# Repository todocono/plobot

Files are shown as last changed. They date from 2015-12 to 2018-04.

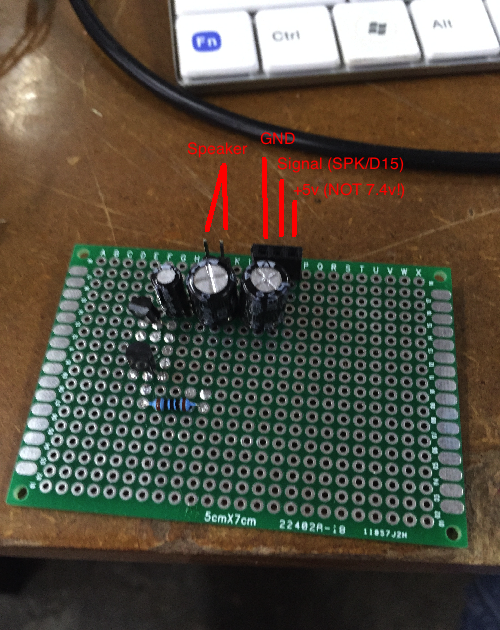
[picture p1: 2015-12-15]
audio_test/prototype.png

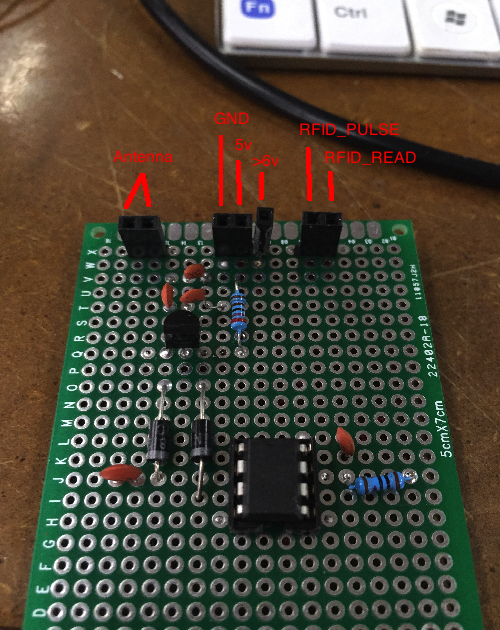
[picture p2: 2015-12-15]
RFIDTest/prototype.png

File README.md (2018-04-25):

# ATTENTION: Files here are deprecated

Plobot is a project started in 2015 by Camilo Parra Palacios and Rodolfo Cossovich. The project website is hosted at http://plobot.com

This repository had various contributors, mainly Sean, Ivan and Arlen. I moved files for maintenance to the repositories:

https://github.com/todocono/Plobot-PCB
https://github.com/todocono/Plobot-ID
https://github.com/todocono/Plobot-soft

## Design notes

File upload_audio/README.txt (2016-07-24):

To write a binary file to the Plobot's flash chip on OSX: 

1. Connect FTDI. Have bootloader installed on Atmega644P. 
2. Upload arduino_stream.ino to the Atmega644P. 
3. Run "goSerial". Set modem port (/dev/something) to 57600 baud rate and press connect
	Note that you should see "---- Streaming Upload ready ----" in the window.
4. Build + run upload_stream.cc
	For example: g++ -o upload_stream ./upload_stream.cc
				 upload_stream ../audio_test/mambo.pcm /dev/cu.usbmodem1421 NORMAL
5. Watch goSerial for error messages. Note that "unknown command" means that the XSP device needs an initial character to get it out of command mode. Use "XSP" instead of "NORMAL" in your upload_stream command.

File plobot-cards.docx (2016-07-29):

Card functions

English | 名字 | Spanish | Description | Special Function
Start | 开始 | Empezar | Starts the sequential program | n/a
Reset | 重置 | Resetear | Pauses the execution of the program. If it is not running, it will clear the memory. | n/a
Go Ahead | 前进 | Adelante | Moves one step forward (about 15cm) | Moves a small step forward ( 5cm?)
Turn Left | 左转 | Gira a la izquierda | Turns 90 degrees left | Turns a small step (15 degrees)
Turn Right | 右转 | Gira a la derecha | Turns 90 degrees right | Turns a small step (15 degrees)
Go Back | 后退 | Atras | Moves one step backward (about 15cm) | Moves a small step backward ( 5cm?)
Lift | 手臂 | Levantar | Toggles both servos position 0/ 90 /90 degrees. | Toggles both servos position within 15 degrees . Till 180 and comes back
Listen | 听 | Escuchar | It has a logic output of YES/NO referred to a clap | It has the opposite logic
See | 探测 | Detectar | It has a logic output of YES/NO referred to a 5cm obstacle | It has the opposite logic
Feel | 触摸 | Sentir | It has a logic output of YES/NO referred to a big inclination change (shake or double tap would work) | It has the opposite logic

Note 1: colors combine with each other. Intensity modifies if followed by a value.

Note 2: (for future versions) all parameters are normalized between a 0 and 10, or a min and max. In the case of musical notes Do, Re, Mi, Fa, Sol, La, Si and Do, Re, Mi of the following octave.

Note 3: Servos are detached when not moving.

Note 4: Need a visual/audio indication when: card is read, program is executing, battery is low

Spells

Repeat | 重复 | Repetir | It reproduces a chunk of code. If followed by a sequence of store/code/store, it redefines the function. If it has a repeat inside of it's own definition, it loops forever. | idem
Store | 储存 | Guardar | If preceded by Repeat, Starts / ends the content of Repeat function. It works as brackets. If preceded by Sound, it stores a sound in the internal memory. | idem
Random | 随机 | Azar | Gives a random number that affects the behavior of the last order.
Teach | 教学 | Enseñar | Teaches a set of movements
Boost | 更改 | Especial | Modifies other functions. It stays ON only for one card. It modifies the way that the light glows. | Sets Boost like a caps lock.
Pause / Freeze | 暂停 | Pausa | Waits for 1s | Waits for 10s
Sound | 声音 | Sonido | Alone, it plays the sound recorded. If followed by Store, allows to save a new recorded sound. | It has some pre-recorded sounds.

7 colors of rainbow

Red | 红色 | Rojo | Turns ON led to glow Red. | Blinking Red
Green | 绿色 | Verde | Turns ON led to glow Green | Blinking Green
Orange | 橙色 | Naranja | Turns ON led to glow | Blinking
Yellow | 黄色 | Amarillo | Turns ON led to glow | Blinking
Pink | 靛蓝 | Rosa | Turns ON led to glow | Blinking
Purple | 紫色 | Violeta | Turns ON led to glow | Blinking
Blue | 蓝色 | Azul | Turns ON led to glow Blue | Blinking Blue

7 notes of music

do | do | | Piano do | Bemol or Sharp?
re | re
mi | mi
fa | fa
sol | sol
la | la
si | si

learning by demonstration

similar to behavior

demonstrating the kinetic

mode to teach the robot movements

custom capabilities

IMU with encoders

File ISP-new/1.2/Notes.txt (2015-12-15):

2011.08.26:
	- Para programar DuinoBot.v1.x con el AVRDoper que está en RobotGroup, utilizar el siguiente BAT:
		DuinoBot.bat
		
	- Para programar DuinoBot.v1.x el USBasp mío, utilizar el siguiente BAT:
		DuinoBot.USBAsp.bat
		
	- Para programar DuinoBot.Kids.v1.x con el AVRDoper que está en RobotGroup, utilizar el siguiente BAT:
		- Kids.bat

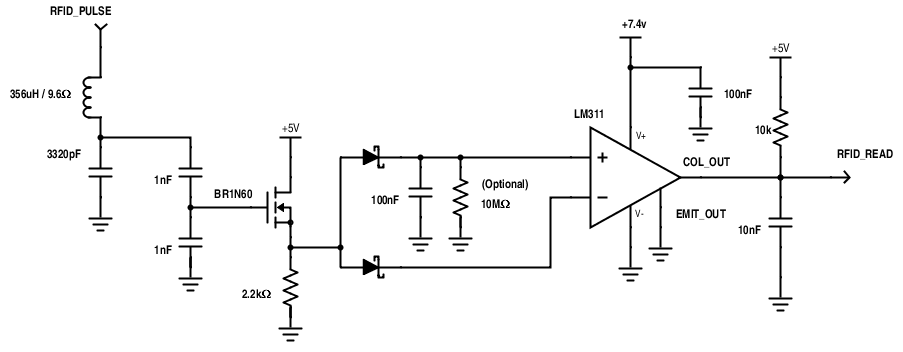
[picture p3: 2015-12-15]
RFIDTest/schematic.png

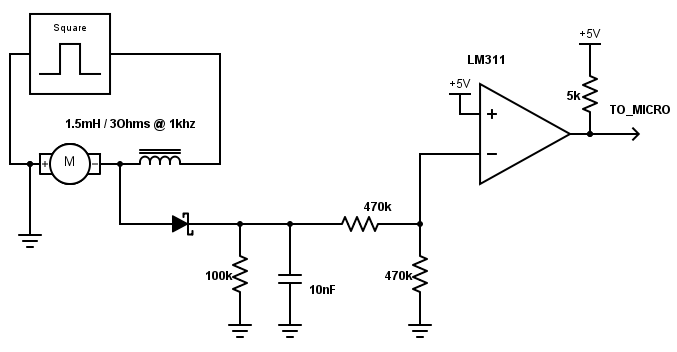
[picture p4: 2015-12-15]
back_emf_test/circuit_schematic.png

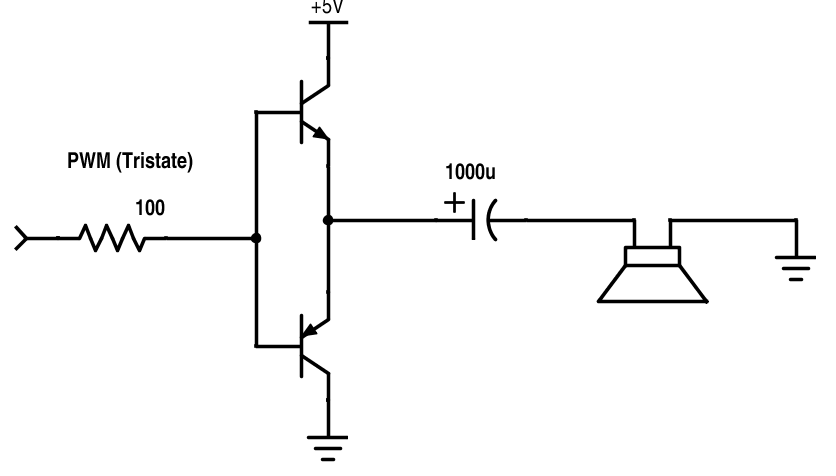
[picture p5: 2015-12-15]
audio_test/schematic.png

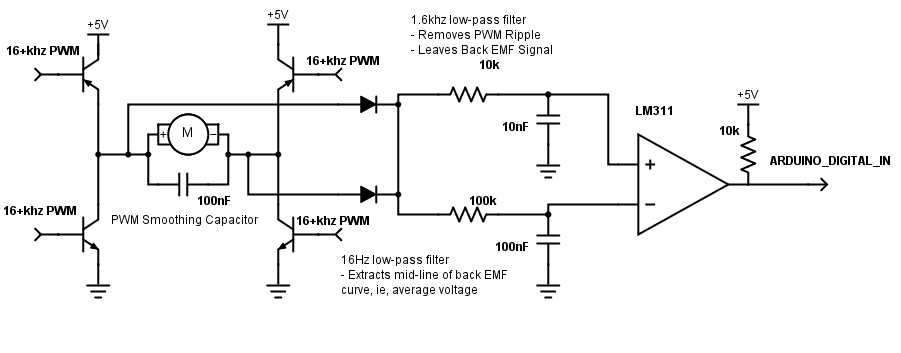
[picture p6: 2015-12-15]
Back-EMF-Sense.png

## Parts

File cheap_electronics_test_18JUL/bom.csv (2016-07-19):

Comment | Description | Designator | Footprint | LibRef | Quantity
18pF | Capacitor | C1, C4 | CAPC1608N | Cap | 2
10uF | Capacitor | C2, C3 | CAPC1608N | Cap | 2
10uF | Capacitor | C5, C? | CAPC3216L | Cap | 2
100nF | Capacitor | C6, C7 | CAPC1608N | CAP | 2
3320pF | Capacitor | C8 | CAPC1608N | Cap | 1
1uF | Capacitor | C9 | CAPC1608N | Cap | 1
MBR0540 | Default Diode | D1, D2, D3, D5, D6, D7, D8, D9 | SOD123/X.85 | Diode | 8
LED3 | Typical BLUE SiC LED | D4 | CAPC1608N | LED3 | 1
XSP | Header, 4-Pin, Dual row, Right Angle | J1 | HDR2X4H | Header 4X2H | 1
Header 2H | Header, 2-Pin, Right Angle | JANT (1, JLOAD1, JPWR1 | HDR1X2H | Header 2H | 3
Header 5H | Header, 5-Pin, Right Angle | JDBG1 | HDR1X5H | Header 5H | 1
BSS806N |  | Q1, Q2, Q3, Q4, Q5, Q6, Q7, Q8, Q9, Q10, Q11 | BSS806N | BSS806N | 11
10k | Resistor | R1, R2, R11, R12, R20 | RESC1608N | Res2 | 5
300 | Resistor | R3 | RESC1608N | Res2 | 1
100 | Resistor | R4, R5, R6, R8, R9, R13, R14, R15, R21 | RESC1608N | Res2 | 9
10 | Resistor | R7 | RESC1608N | Res2 | 1
50 | Resistor | R10 | RESC1608N | Res2 | 1
100k | Resistor | R16 | RESC1608N | Res2 | 1
1k | Resistor | R17, R18, R19 | RESC1608N | Res2 | 3
ATmega644A-AU | 8-bit AVR Microcontroller, 64KB Flash, 2KB EEPROM, 4KB SRAM, 44-pin TQFP, Industrial Grade (-40°C to 85°C) | U1 | 44A_N | ATmega644A-AU | 1
ABM7-8.000MHZ-D2Y-T |  | XTAL1 | XTAL | ABM7-8.000MHZ-D2Y-T | 1

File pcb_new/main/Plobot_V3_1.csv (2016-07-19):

Comment | Description | Designator | Footprint | LibRef | Quantity
ON/OFF |  | B1 | KGPS22F03 | Component_1 | 1
100nF | Capacitor | C1, C3, C6, C7, C8, C12, C13, C14, C15, C16, C18, C19, C21, C26, C27, C28, C29, C32, C34, C35, C37, C38, C48 | CAPC1608N | Cap | 25
18pF | Capacitor | C2, C4 | CAPC1608N | Cap | 2
10 uF | Capacitor | C5, C11 | CAPC3216N | Cap_2 | 2
15pF | Capacitor | C9, C10, C22, C45 | CAPC1608N | CAP | 4
10uF | Capacitor | C17, C23, C31, C51 | CAPC3216N | Cap_2 | 4
47pF | Capacitor | C24, C42 | CAPC1608N | CAP | 2
10nF/16V | Capacitor | C25, C33 | CAPC2012N | Cap | 2
2.2uF | Capacitor | C30, C39 | CAPC2012N | Cap, Cap_2 | 2
1uF | Capacitor | C36 | CAPC2012N | Cap_2 | 1
180pF | Capacitor | C40, C43 | CAPC1608N | CAP | 2
10pF | Capacitor | C41, C44 | CAPC1608N | CAP | 2
MBR0540 | Default Diode | D1 | SOD123/X.85 | Diode | 1
LED3 | Typical BLUE SiC LED | DLED | LED 0603/1608 BLUE | LED3 | 1
miniSMDC260F/12 | Thermal Fuse | F1, F2 | miniSMDC260F/12 | Fuse Thermal | 2
XSP | Header, 4-Pin, Dual row, Right Angle | J1 | HDR2X4H | Header 4X2H | 1
Header 15 | Header, 15-Pin | JBOTTOM | B15B-XH-A | Header 15 | 1
Charger |  | JCHG1 | S3B-XH-A(LF)(SN) | BATTCON | 1
Header 5 | Header, 5-Pin | JDBG | HDR1X5 | Header 5 | 1
Header 4 | Header, 4-Pin | JI2C, JSPI | HDR1X4 | Header 4 | 2
Header 7 | Header, 7-Pin | JTOP | B7B-XH-A | Header 7 | 1
10uH | Inductor | L1 | INDC1608N | Inductor | 1
2.2uH | Inductor | L2, L3 | INDC1608N | Inductor | 2
Mic2 | Microphone | MK1 | electret_6mm | Mic2 | 1
10k | Resistor | R1, R2, R4, R5, R6, R7, R9, R12, R13, R14, R17, R18, R22 | RESC1608N | Res2 | 13
20k | Resistor | R3 | RESC1608N | Res2 | 1
100k | Resistor | R8 | RESC1608N | Res2 | 1
3.3k | Resistor | R10 | RESC1608N | Res2 | 1
22 | Resistor | R11 | RESC1608N | Res2 | 1
820 | Resistor | R15 | RESC1608N | Res2 | 1
5.1k | Resistor | R16, R20, R21 | RESC1608N | Res2 | 3
1K | Resistor | R19, R23 | RESC1608N | Res2 | 2
470 | Resistor | R27 | RESC1608N | Res2 | 1
1 | Resistor | R28 | RESC1608N | Res2 | 1
MCU | 8-bit AVR Microcontroller, 2.7-5.5V, 20MHz, 64KB Flash, 2KB EEPROM, 4KB SRAM, 44-pin TQFP | U1 | atmega644p | ATmega644-20AU | 1
LM358D | Dual Operational Amplifier | U2 | LM358D | LM358D | 1
W25Q64BVSIG |  | U3 | W25Q64BVSIG | W25Q64BVSIG | 1
SN74HC04D | Hex Inverter | U4 | D014_N | SN74HC04D | 1
AZ1117CH-3.3 |  | U5 | SOT223 | LM1117 | 1
SN74HC08D | Quadruple 2-Input Positive-AND Gate | U8, U14 | D014_N | SN74HC08D | 2
DRV8833 |  | U9, U12 | DRV8833 | DRV8833 | 2
ITR9608 + 2x 额外的塑料片 |  | U10, U11 | ITR9608 | ITR9608 + 2x 额外的塑料片 | 2
ADXL345BCCZ |  | U13 | ADXL345 | ADXL345 | 1
AZ1084CD-5.0 |  | U101 | AZ1084CD-5.0 | AZ1084CD-5.0 | 1
WS2812B |  | ULED_INNER, ULED_OUTER1, ULED_OUTER2, ULED_OUTER3, ULED_OUTER4 | WS2812B | WS2812B | 5
MFRC52202HN1 |  | URFID | MFRC52202HN1 | MFRC52202HN1 | 1
7A-27.120MAAJ-T |  | XRFID | XTAL | Tm08B.S01_12M_42 | 1
ABM7-8.000MHZ-D2Y-T |  | XTAL1 | XTAL | ABM7-8.000MHZ-D2Y-T | 1

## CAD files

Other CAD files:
pcb_mechanical.DXF

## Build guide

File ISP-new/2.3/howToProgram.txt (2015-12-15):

::DuinoBot.v2.3::

1. First program the ATMega16U2: connect the USBasp to its ISP connector, and run DuinoBot.mega16U2.USBAsp.bat.
2. Second program the ATMega1284p: connect the USBasp to its ISP connector, and run DuinoBot.mega1284.USBAsp.bat.
3. Finally, run the test protocol with DuinoPack.v1.0 (can be downloaded from this link: http://multiplo.org/category/software/).

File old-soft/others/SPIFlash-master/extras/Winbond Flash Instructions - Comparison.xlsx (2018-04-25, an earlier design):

Characteristics | W25X05CL | W25X10BV | W25X20BV | W25X40BV | W25Q80BV | W25Q16BV | W25Q32BV | W25Q64BV | W25Q128BV | W25Q256FV
Size (Bits) | 512K-Bit | 1M-Bit | 2M-Bit | 4M-Bit | 8M-Bit | 16M-Bit | 32M-Bit | 64M-Bit | 128M-Bit | 256M-Bit
Size (Bytes) | 64K-Byte | 128K-Byte | 256K-Byte | 512K-Byte | 1M-Byte | 2M-Byte | 4M-Byte | 8M-Byte | 16M-Byte | 32M-Byte
Programming size | 64L*1024L | 128L*1024L | 256L*1024L | 512L*1024L | 1L*1024L*1024L | 2L*1024L*1024L | 4L*1024L*1024L | 8L*1024L*1024L | 16L*1024L*1024L | 32L*1024L*1024L
No. of pages | 256 | 512 | 1024 | 2048 | 4096 | 8192 | 16384 | 32768 | 65536 | 131072
Voltage | 2.5V - 3.3V | 2.7V - 3.6V | 2.7V - 3.6V | 2.7V - 3.6V | 2.5V - 3.6V | 2.7V to 3.6V | 2.7V to 3.6V | 2.7V to 3.6V | 2.7V to 3.6V | 2.7V to 3.6V
Current (Active) | 1mA | 4mA | 4mA | 4mA | 4mA | 4mA | 4mA | 4mA | 4mA | 4mA
Current (Power-down) | < 1µA | < 1µA | < 1µA | < 1µA | < 1µA | < 1µA | < 1µA | < 1µA | < 1µA | < 1µA
Sector size | 4KB | 4KB | 4KB | 4KB | 4KB | 4KB | 4KB | 4KB | 4KB | 4KB
No. of sectors | 16 | 32 | 64 | 128 | 256 | 512 | 1024 | 2048 | 4096 | 8192
No. of 32K blocks | 2 | 4 | 8 | 16 | 32 | 64 | 128 | 256 | 512 | 1024
No. of 64K blocks | 1 | 2 | 4 | 8 | 16 | 32 | 64 | 128 | 256 | 512
I/O | SPI, DUAL I/O | SPI, Dual Outputs, Dual I/O | SPI, Dual Outputs, Dual I/O | SPI, Dual Outputs, Dual I/O | SPI, Dual SPI, Quad SPI | SPI, Dual SPI, Quad SPI | SPI, Dual SPI, Quad SPI | SPI, Dual SPI, Quad SPI | SPI, Dual SPI, Quad SPI | SPI, Dual SPI, Quad SPI
Max clock speed | 104MHz | 104MHz | 104MHz | 104MHz | 104MHz | 104MHz | 104MHz | 80MHz | 104MHz
Page Program | YES | YES | YES | YES | YES | YES | YES | YES | YES | YES
Identification
Manufacturer ID | EFh | EFh | EFh | EFh | EFh | EFh | EFh | EFh | EFh | EFh
Device ID
Byte 1 (Manufacturer ID) | EFh | EFh | EFh | EFh | EFh | EFh | EFh | EFh | EFh | EFh
Byte 2 (Memory Type) | 05h | 10h | 11h | 12h | 13h | 14h | 15h | 16h | 17h | 18h
Byte 3 (Capacity) | 3010h | 3011h | 3012h | 3013h | 4014h | 4015h | 4016h | 4017h | 4018h | 4019h
Instructions
Write Enable | 06h | 06h | 06h | 06h | 06h | 06h | 06h | 06h | 06h | 06h
Write Enable for Volatile Status Register | 50h | - | - | - | 50h | - | 50h | - | 50h | 50h
Write Disable | 04h | 04h | 04h | 04h | 04h | 04h | 04h | 04h | 04h | 04h
Read Status Register 1 | 05h | 05h | 05h | 05h | 05h | 05h | 05h | 05h | 05h | 05h
Read Status Register 2 | - | - | - | - | 35h | 35h | 35h | 35h | 35h | 35h
Write Status Register 1 | 01h | 01h | 01h | 01h | 01h | 01h | 01h | 01h | 01h | 01h
Write Status Register 2 |  |  |  |  |  |  |  |  |  | 31h
Write Status Register 3 |  |  |  |  |  |  |  |  |  | 11h
Read Extended Addr. Register |  |  |  |  |  |  |  |  |  | C8h
Write Extended Addr. Register |  |  |  |  |  |  |  |  |  | C5h
Read Data | 03h | 03h | 03h | 03h | 03h | 03h | 03h | 03h | 03h | 03h
Fast Read | 0Bh | 0Bh | 0Bh | 0Bh | 0Bh | 0Bh | 0Bh | 0Bh | 0Bh | 0Bh
Fast Read Dual Output | 3Bh | 3Bh | 3Bh | 3Bh | 3Bh | 3Bh | 3Bh | 3Bh | 3Bh | 3Bh
Fast Read Dual I/O | BBh | BBh | BBh | BBh | BBh | BBh | BBh | BBh | BBh | BBh
Fast Read Quad Output | - | - | - | - | 6Bh | 6Bh | 6Bh | 6Bh | 6Bh | 6Bh
Fast Read Quad I/O | - | - | - | - | EBh | EBh | EBh | EBh | EBh | EBh
Word Read Quad I/O | - | - | - | - | E7h | E7h | E7h | - | E7h | E7h
Octal Word Read Quad I/O | - | - | - | - | E3h | E3h | E3h | E3h | E3h | E3h
Set Burst with wrap | - | - | - | - | 77h | - | 77h | - | 77h | 77h
Page Program | 02h | 02h | 02h | 02h | 02h | 02h | 02h | 02h | 02h | 02h
Quad Page Program | - | - | - | - | 32h | 32h | 32h | 32h | 32h | 32h
Sector Erase (4KB) | 20h | 20h | 20h | 20h | 20h | 20h | 20h | 20h | 20h | 20h
Block Erase (32KB) | 52h | 52h | 52h | 52h | 52h | 52h | 52h | 52h | 52h | 52h
Block Erase (64KB) | D8h | D8h | D8h | D8h | D8h | D8h | D8h | D8h | D8h | D8h
Chip Erase | C7h/60h | C7h/60h | C7h/60h | C7h/60h | C7h/60h | C7h/60h | C7h/60h | C7h/60h | C7h/60h | C7h/60h
Erase/Program suspend | - | - | - | - | 75h | 75h | 75h | 75h | 75h | 75h
Erase/Program resume | - | - | - | - | 7Ah | 7Ah | 7Ah | 7Ah | 7Ah | 7Ah
Contiuous Read Mode | - | - | - | - | FFh | FFh | FFh | FFh | FFh | FFh
High Performance Mode | - | - | - | - | - | - | - | A3h | - | -
Power-down | B9h | B9h | B9h | B9h | B9h | B9h | B9h | B9h | B9h | B9h
Release Power-down/ Device ID | ABh | ABh | ABh | ABh | ABh | ABh | ABh | ABh | ABh | ABh
Manufacturer/Device ID | 90h | 90h | 90h | 90h | 90h | 90h | 90h | 90h | 90h | 90h
Manufacturer/Device ID by Dual I/O | 92h | 92h | 92h | 92h | 92h | 92h | 92h | - | 92h | 92h
Manufacturer/Device ID by Quad I/O | - | - | - | - | 94h | 94h | 94h | - | 94h | 94h
JEDEC ID | 9Fh | 9Fh | 9Fh | 9Fh | 9Fh | 9Fh | 9Fh | 9Fh | 9Fh | 9Fh
Read Unique ID | 4Bh | 4Bh | 4Bh | 4Bh | 4Bh | 4Bh | 4Bh | 4Bh | 4Bh | 4Bh
Read SDFP Register | - | - | - | - | 5Ah | - | 5Ah | - | 5Ah
Erase Security Registers | - | - | - | - | 44h | - | 44h | - | 44h
Program Security Registers | - | - | - | - | 42h | - | 42h | - | 42h
Read Security Registers | - | - | - | - | 48h | - | 48h | - | 48h
Global Block Lock |  |  |  |  |  |  |  |  |  | 7Eh
Global Block Unlock |  |  |  |  |  |  |  |  |  | 98h
Individual Block Lock |  |  |  |  |  |  |  |  |  | 36h
Individual Block Unlock |  |  |  |  |  |  |  |  |  | 39h
Read Block Lock |  |  |  |  |  |  |  |  |  | 3Dh

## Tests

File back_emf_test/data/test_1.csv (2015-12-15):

EMF | Encoder
101.00 | 26.00
416.00 | 29.00
874.00 | 40.00
1222.00 | 52.00
1552.00 | 63.00
1836.00 | 77.00
2172.00 | 89.00
2462.00 | 101.00
2760.00 | 113.00
3074.00 | 125.00
3366.00 | 138.00
3688.00 | 150.00
4042.00 | 165.00
4417.00 | 180.00
1.00 | 7.00
0.00 | 0.00
0.00 | 0.00
0.00 | 0.00
0.00 | 0.00
0.00 | 0.00
0.00 | 0.00
1746.00 | 72.00
2048.00 | 86.00
2412.00 | 99.00
2736.00 | 112.00
3050.00 | 125.00
3322.00 | 136.00
3660.00 | 149.00
4040.00 | 165.00
4370.00 | 179.00
2.00 | 9.00
0.00 | 0.00
0.00 | 0.00
0.00 | 0.00
0.00 | 0.00
0.00 | 0.00
0.00 | 0.00
0.00 | 0.00
782.00 | 32.00
1162.00 | 47.00
1196.00 | 45.00
1530.00 | 57.00
1860.00 | 69.00
1974.00 | 76.00
2336.00 | 89.00
2564.00 | 99.00
0.00 | 2.00
0.00 | 0.00
0.00 | 0.00
0.00 | 0.00
620.00 | 27.00
830.00 | 34.00
1068.00 | 42.00
1286.00 | 49.00
1554.00 | 59.00
2212.00 | 87.00
3124.00 | 130.00

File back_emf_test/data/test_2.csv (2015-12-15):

EMF | Encoder
0.00 | 0.00
0.00 | 0.00
0.00 | 0.00
0.00 | 0.00
1640.00 | 67.00
1991.00 | 82.00
2255.00 | 92.00
2526.00 | 104.00
2891.00 | 118.00
3193.00 | 132.00
3500.00 | 143.00
3769.00 | 155.00
4133.00 | 169.00
4496.00 | 185.00
0.00 | 7.00
0.00 | 0.00
180.00 | 21.00
482.00 | 32.00
935.00 | 44.00
1291.00 | 54.00
1650.00 | 68.00
2006.00 | 83.00
2262.00 | 92.00
2590.00 | 107.00
2890.00 | 118.00
3204.00 | 132.00
3486.00 | 143.00
3810.00 | 156.00
4194.00 | 171.00
4561.00 | 186.00
1.00 | 7.00
0.00 | 0.00
0.00 | 0.00
0.00 | 0.00
0.00 | 0.00
1326.00 | 59.00
1708.00 | 71.00
1956.00 | 80.00
2188.00 | 90.00
2550.00 | 105.00
2878.00 | 118.00
3228.00 | 131.00
3522.00 | 143.00
3834.00 | 156.00
4174.00 | 171.00
4581.00 | 186.00
1.00 | 8.00
0.00 | 0.00
0.00 | 0.00
0.00 | 0.00
62.00 | 3.00
652.00 | 31.00
674.00 | 28.00
984.00 | 41.00
1220.00 | 50.00
1418.00 | 58.00
1743.00 | 71.00
1861.00 | 76.00
2188.00 | 89.00
2338.00 | 95.00
2483.00 | 102.00
2231.00 | 91.00
0.00 | 3.00
0.00 | 0.00
22.00 | 2.00
254.00 | 12.00
320.00 | 15.00
362.00 | 16.00
464.00 | 20.00
656.00 | 27.00
742.00 | 30.00
802.00 | 32.00
1006.00 | 41.00
864.00 | 34.00
1098.00 | 45.00
1240.00 | 50.00
1244.00 | 51.00
1300.00 | 53.00
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

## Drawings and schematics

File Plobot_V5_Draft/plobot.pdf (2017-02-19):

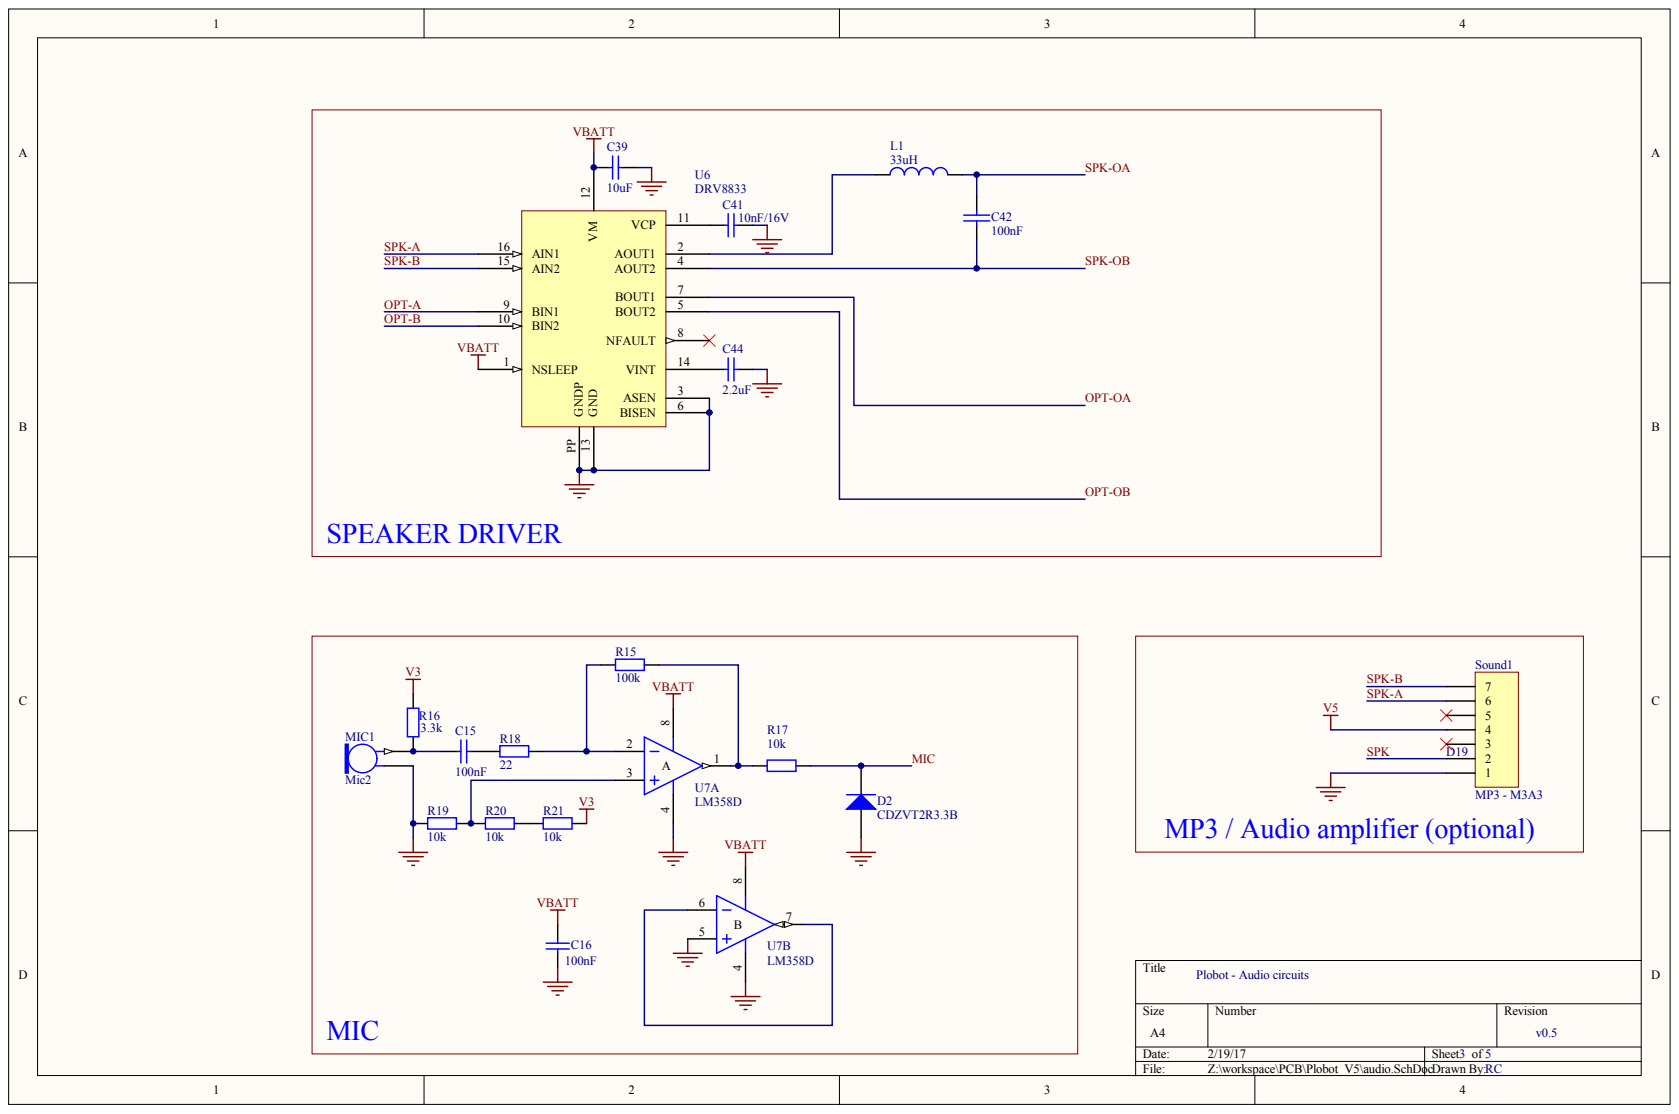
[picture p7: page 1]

Size A4 | Number | Revision v0.5

Date: 2/19/17 | Sheet of 3 5
File: Z:\workspace\PCB\Plobot_V5\audio.SchDocDrawn By: | RC

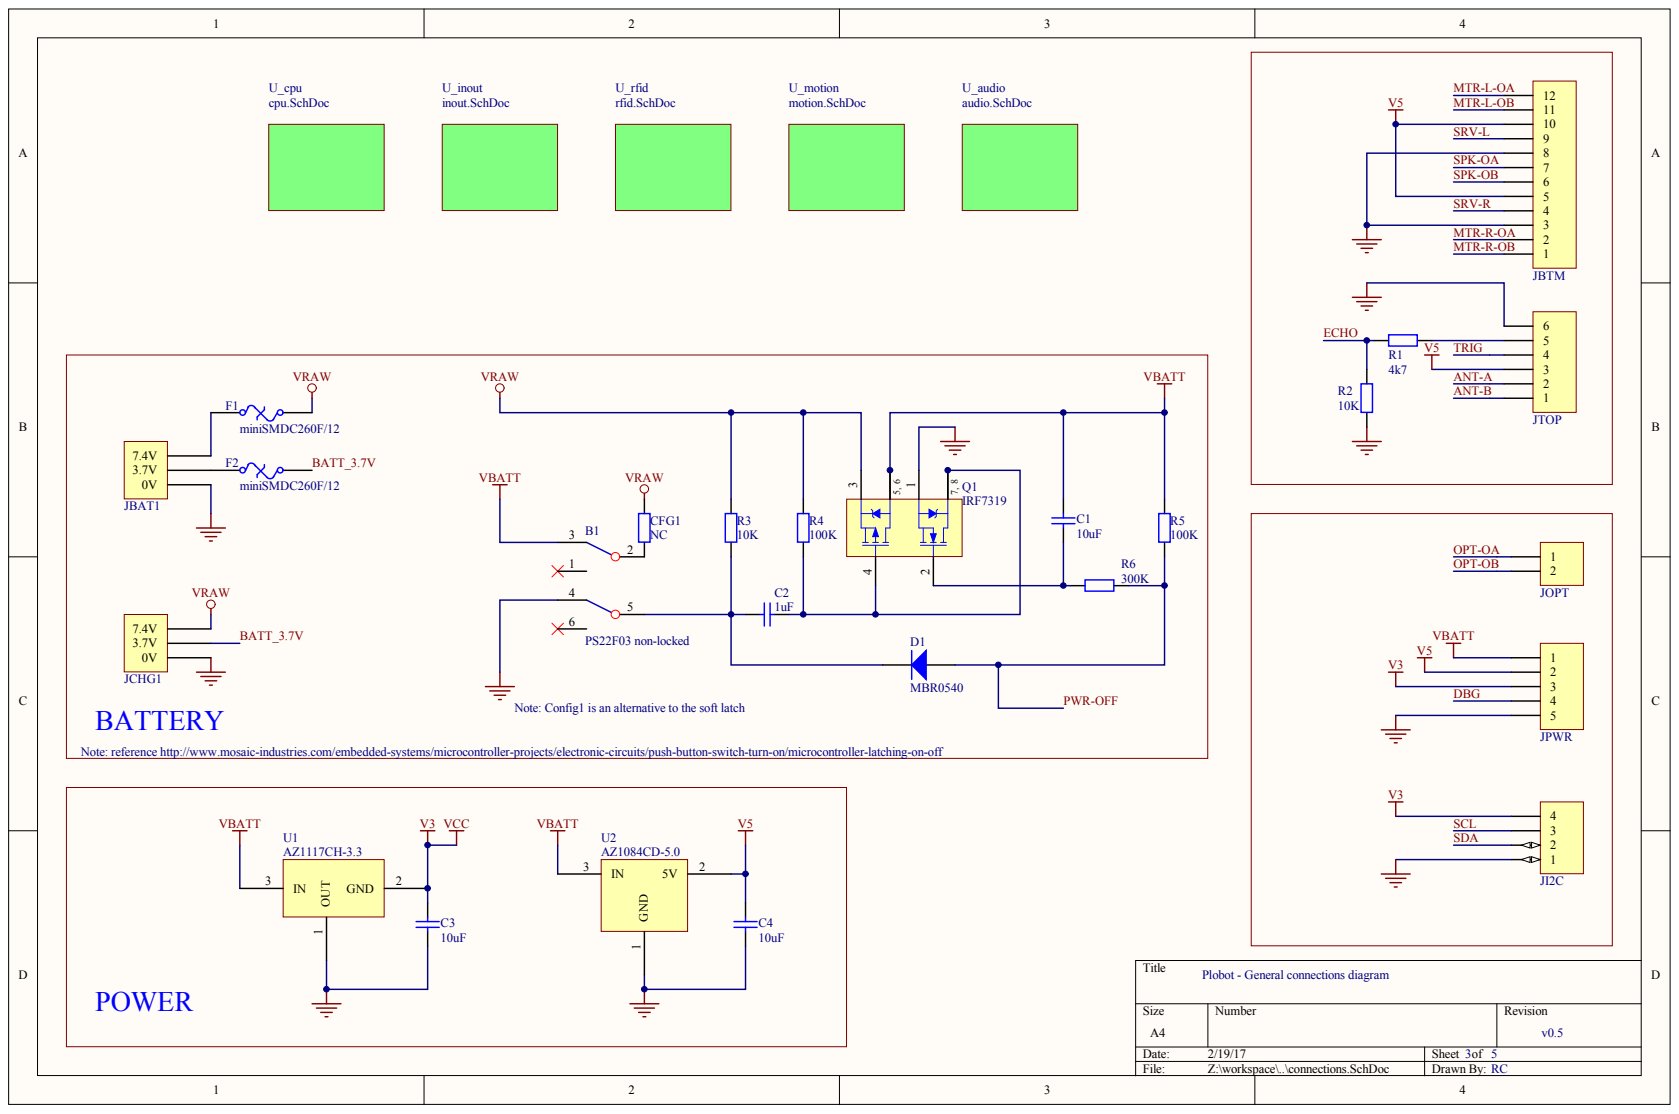
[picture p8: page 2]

Note: Config1 is an alternative to the soft latch

Note: reference http://www.mosaic-industries.com/embedded-systems/microcontroller-projects/electronic-circuits/push-button-switch-turn-on/microcontroller-latching-on-off

Plobot - General connections diagram

Size A4 | Number | Revision v0.5

Date: 2/19/17 | Sheet of 3 5
File: Z:\workspace\..\connections.SchDoc | Drawn By: RC

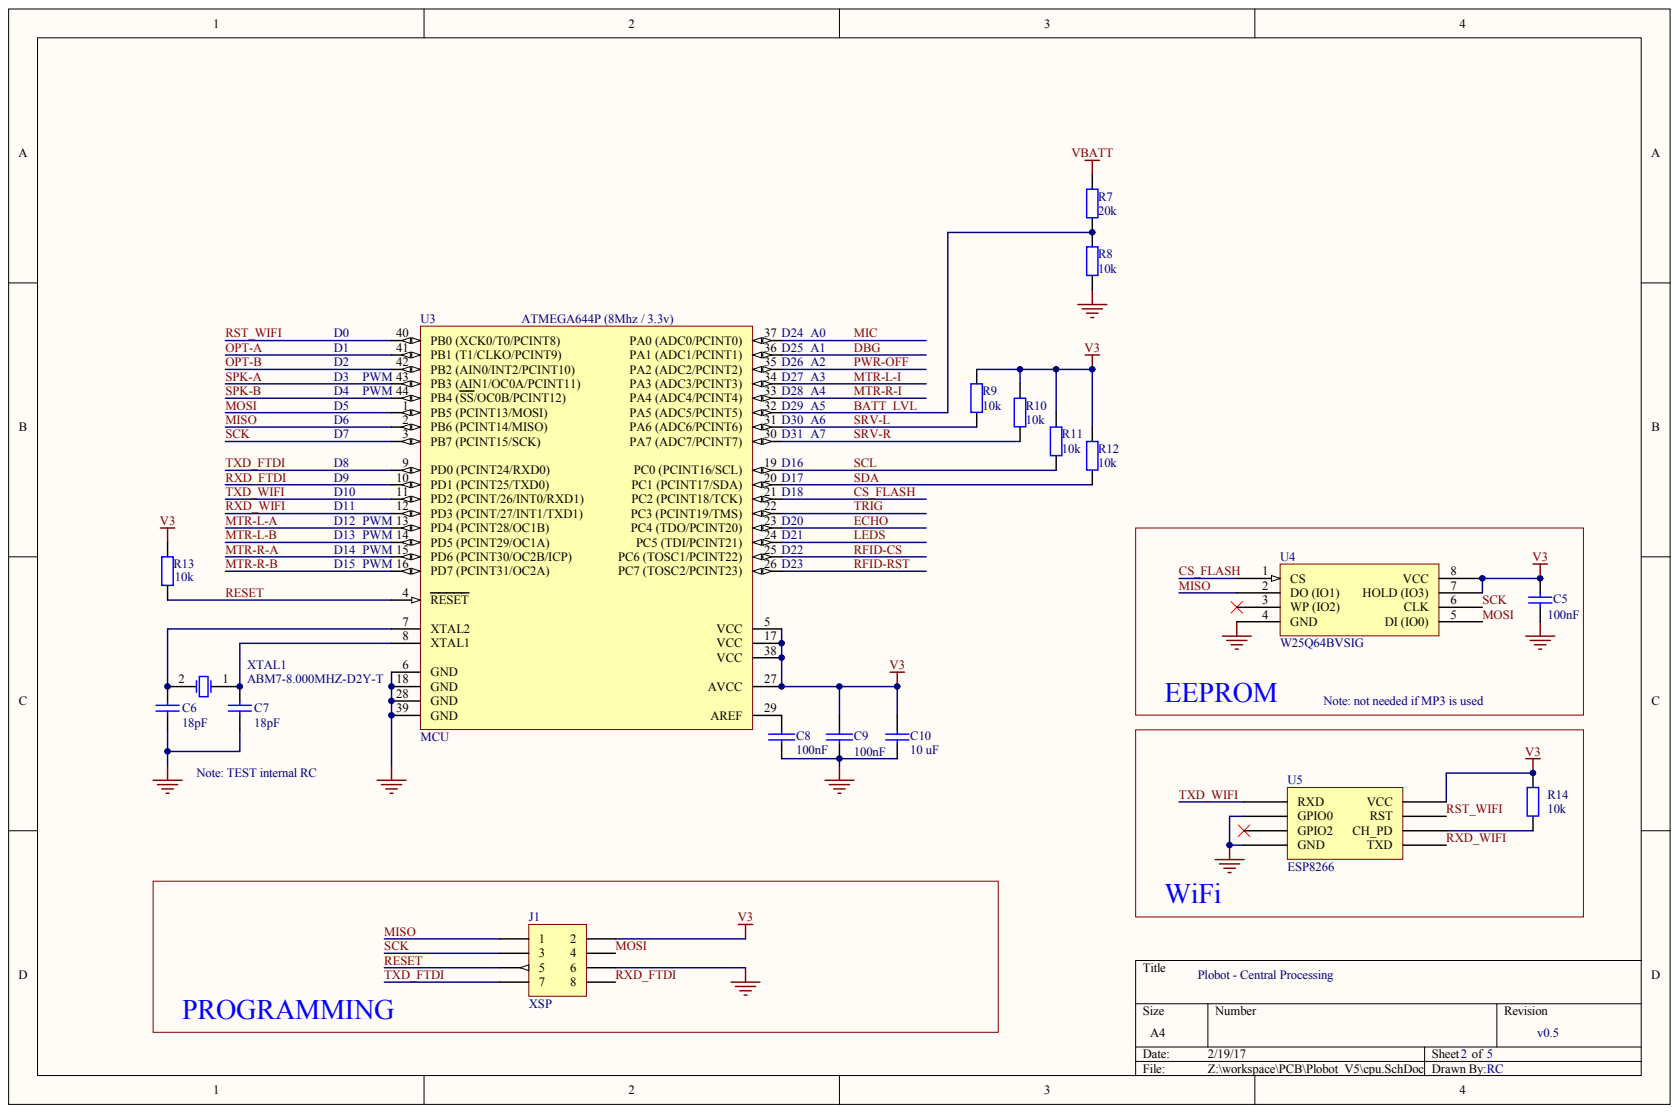
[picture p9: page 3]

D3 0 A 6 SRV-L | 10 k
D3 1 A 7 SRV-R

XTA L 1 ABM7-8.000MHZ-D2Y-T | 6

Si z e A 4 | Numbe r | Rev isi o n v0. 5

Date : 2/19/1 7 | Sh eet o 2 f 5
Fi l e : Z: \workspac e\PCB\ P l obot_V5\cpu.SchDo c | Drawn By : RC

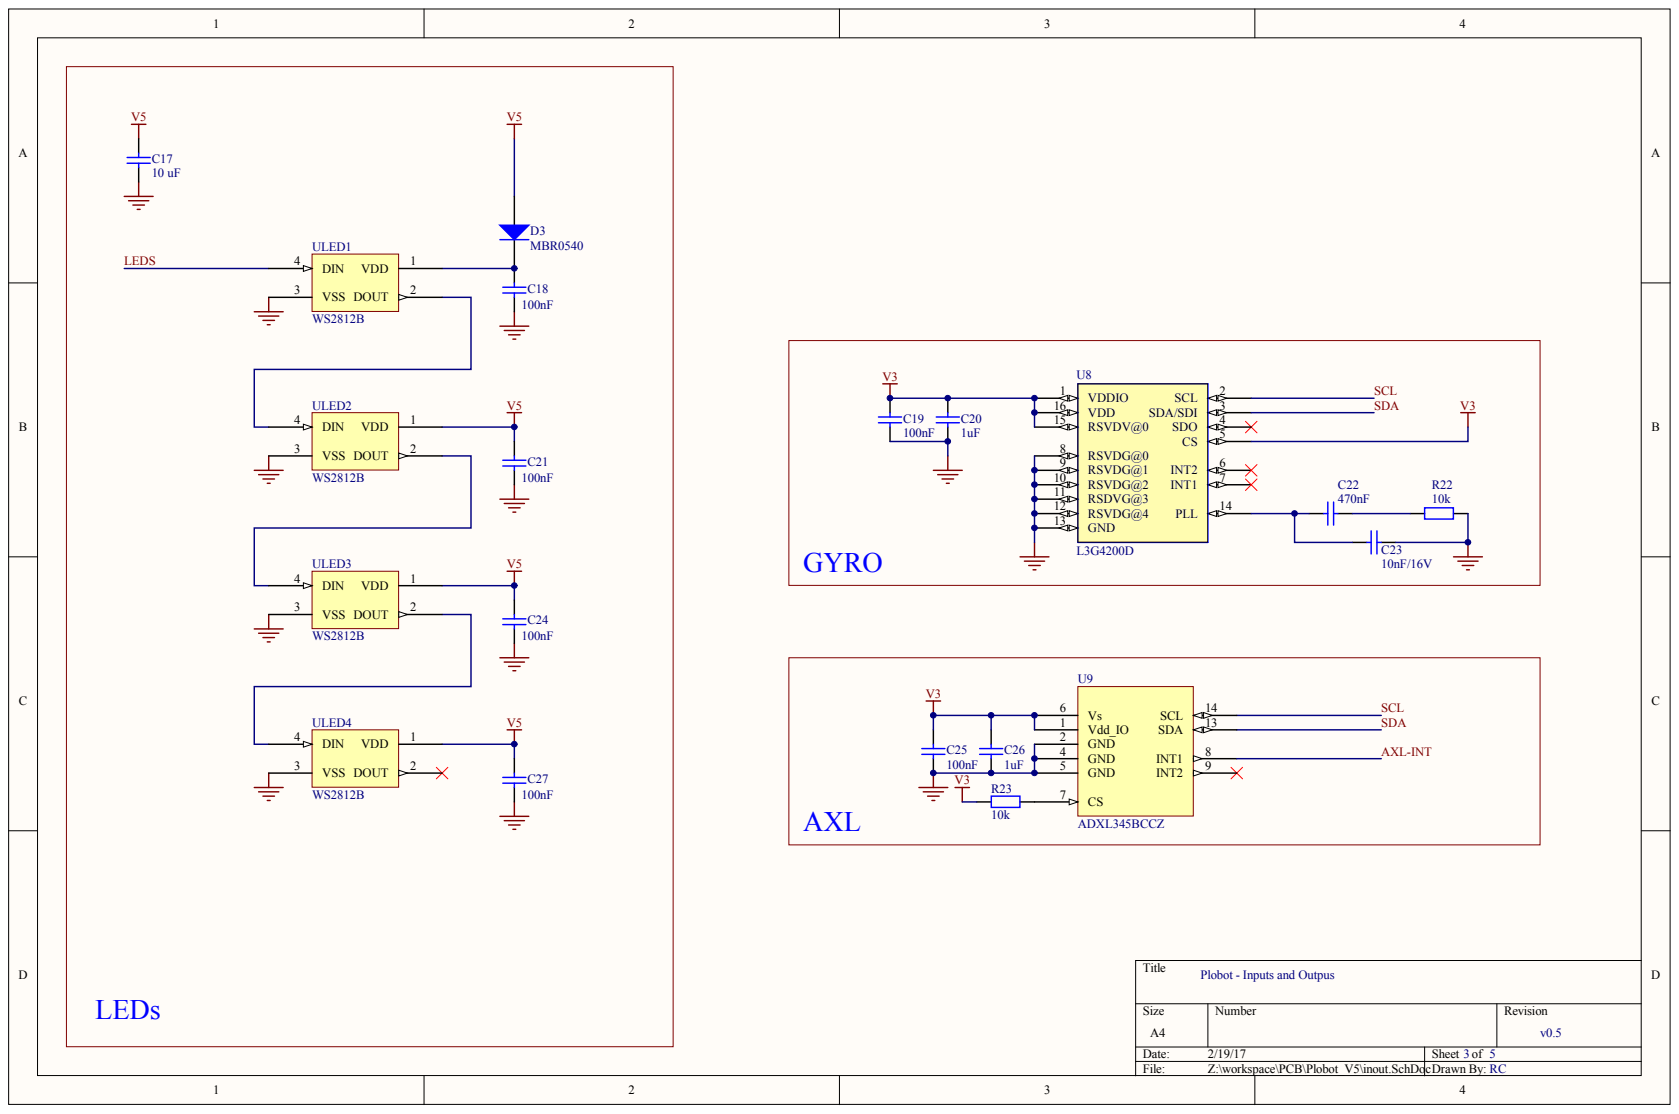
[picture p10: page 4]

Si z e A 4 | Numbe r | Rev isi o n v0. 5

Date : 2/19/1 7 | Sh eet o 3 f 5
Fi l e : Z: \workspac e\PCB\ P l obot_V5\i n out.Sc hDo | cDrawn By : RC

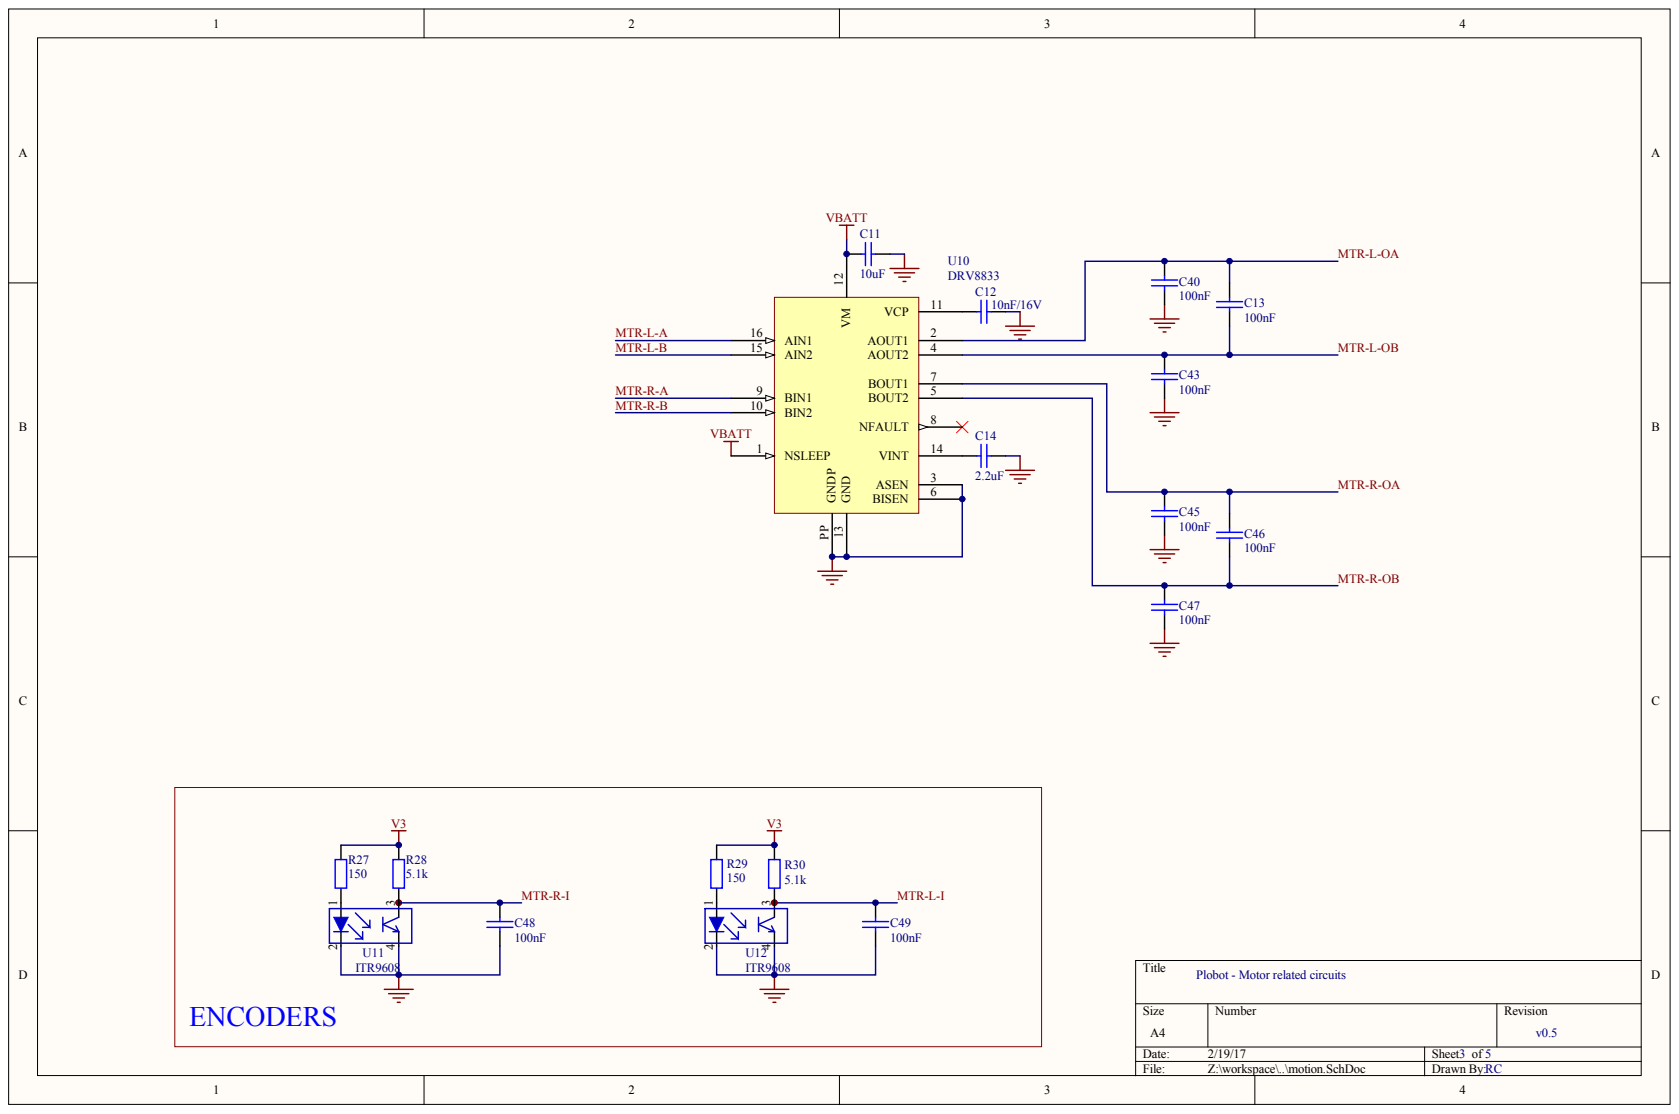
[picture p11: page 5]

Si z e A 4 | Numbe r | Rev isi o n v0. 5

Date : 2/19/1 7 | Sh eet o 3 f 5
Fi l e : Z: \workspac e\..\mo t i o n.Sc hDo c | Drawn By : RC

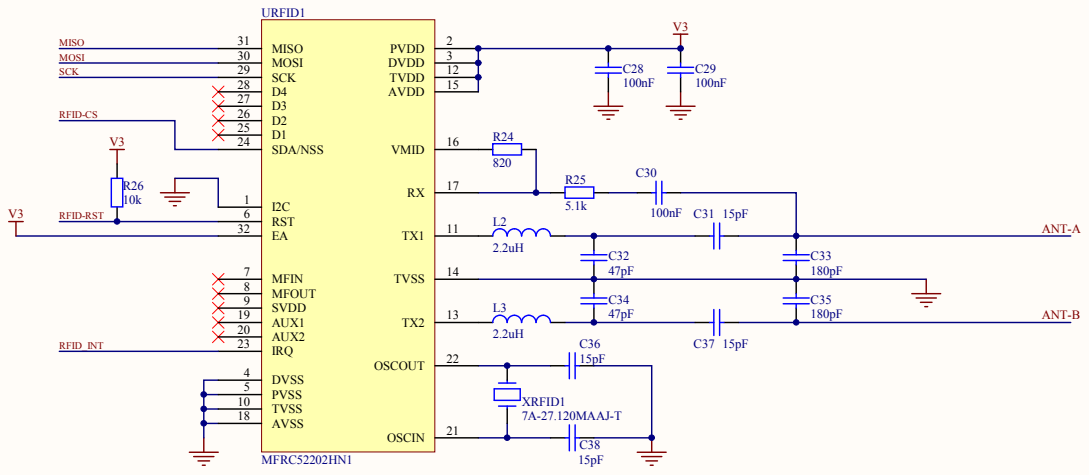
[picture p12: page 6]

TVSS 10 AVSS 18

Si z e A 4 | Numbe r | Rev isi o n v0. 5

Date : 2/19/1 7 | Sh eet o 3 f 5
Fi l e : Z: \workspac e\PCB\ P l obot_V5\rfid.Sc hDo c | Drawn By : RC

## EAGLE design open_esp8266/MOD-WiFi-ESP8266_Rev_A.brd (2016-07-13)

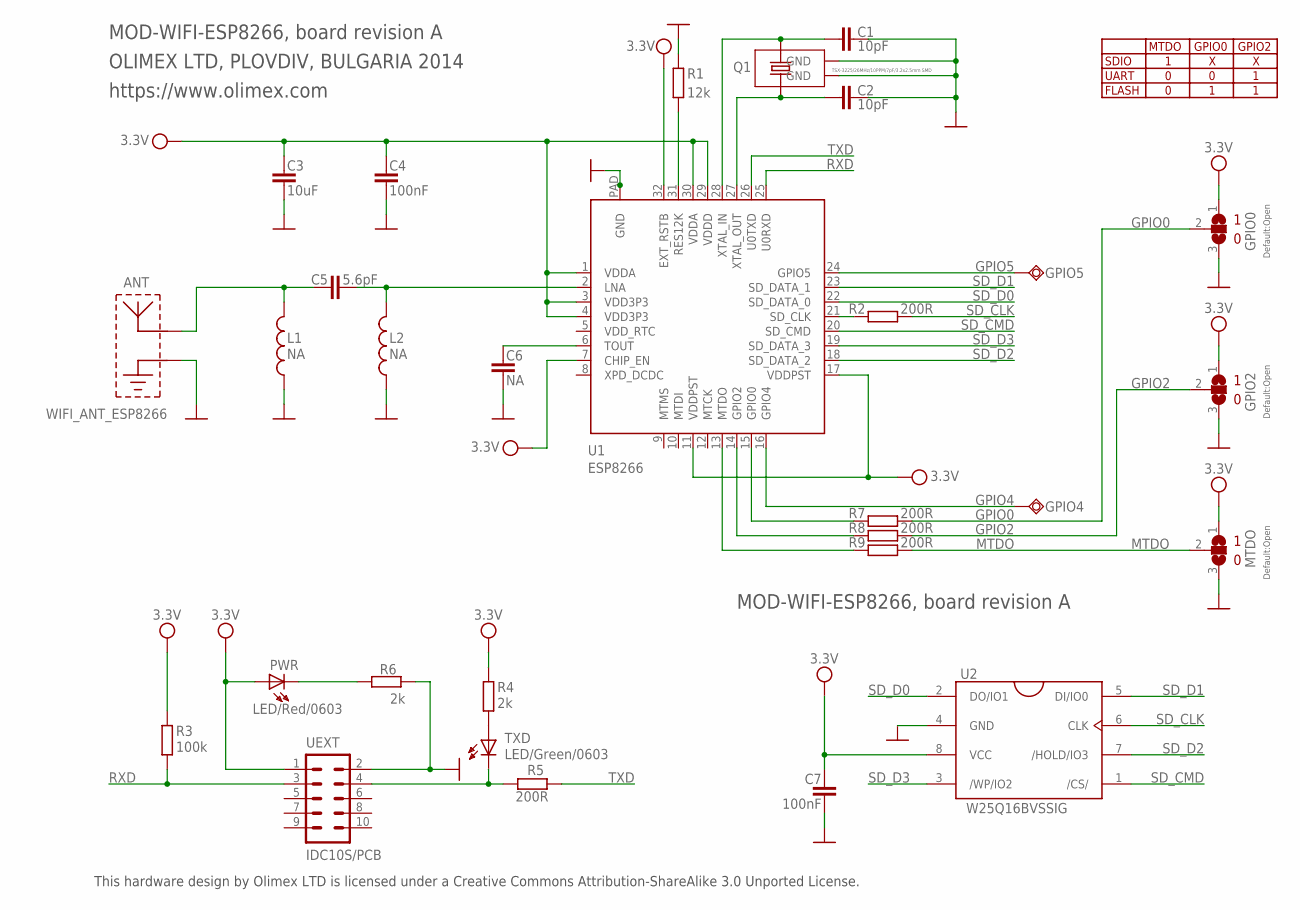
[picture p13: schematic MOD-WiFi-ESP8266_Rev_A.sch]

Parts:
ANT: WIFI_ANT_ESP8266; ESP8266_ANT
C1, C2: 10pF; C0402_TI
C3: 10uF; C0603_DWS
C4, C7: 100nF; C0402_TI
C5: 5.6pF; C0402_TI
C6: NA; C0402_TI
GPIO0, GPIO2: Default:Open; SJ_2_SMALLER
GPIO4, GPIO5: TESTPAD32/56
L1, L2: NA; L0402_TI
MTDO: Default:Open; SJ_2_SMALLER
PWR: LED/Red/0603; LED-0603
Q1: TSX-3225/26MHz/10PPM/7pF/3.2x2.5mm SMD; NX3225SA
R1: 12k; R0402_TI
R2, R5, R7, R8, R9: 200R; R0402_TI
R3: 100k; R0402_TI
R4, R6: 2k; R0402_TI
TXD: LED/Green/0603; LED-0603_L
U1: ESP8266; QFN32_PAD
U2: W25Q16BVSSIG; SO8_ATMEL_FLASH
UEXT: IDC10S/PCB; ML10L_PADS_FEMAIL

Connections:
GND: ANT.GND, C1.1, C2.1, C3.2, C4.2, C6.2, C7.2, GPIO0.3, GPIO2.3, L1.1, L2.1, MTDO.3, Q1.NC_1 (GND), Q1.NC_2 (GND), R1.2, R6.1, U1.P$1 (GND), U1.P$2 (GND), U1.P$3 (GND), U1.P$4 (GND), U1.P$5 (GND), U1.P$6 (GND), U1.P$7 (GND), U1.P$8 (GND), U1.P$9 (GND), U1.PAD (GND), U2.4 (GND), UEXT.2
GPIO0: GPIO0.2, R7.1
GPIO2: GPIO2.2, R8.1
GPIO4: GPIO4.P$1, U1.16 (GPIO4)
GPIO5: GPIO5.P$1, U1.24 (GPIO5)
MTDO: MTDO.2, R9.1
unnamed: R5.2, TXD.C, UEXT.4
unnamed: R4.1, TXD.A
unnamed: PWR.C, R6.2
unnamed: R7.2, U1.15 (GPIO0)
unnamed: R8.2, U1.14 (GPIO2)
unnamed: R9.2, U1.13 (MTDO)
unnamed: C5.2, L2.2, U1.2 (LNA)
unnamed: ANT.ANT, C5.1, L1.2
unnamed: C6.1, U1.6 (TOUT)
unnamed: C2.2, Q1.2, U1.27 (XTAL_OUT)
unnamed: R1.1, U1.31 (RES12K)
unnamed: C1.2, Q1.1, U1.28 (XTAL_IN)
unnamed: R2.2, U1.21 (SD_CLK)
RXD: R3.1, U1.25 (U0RXD), UEXT.3
SD_CLK: R2.1, U2.6 (CLK)
SD_CMD: U1.20 (SD_CMD), U2.1 (/CS/)
SD_D0: U1.22 (SD_DATA_0), U2.2 (DO/IO1)
SD_D1: U1.23 (SD_DATA_1), U2.5 (DI/IO0)
SD_D2: U1.18 (SD_DATA_2), U2.7 (/HOLD/IO3)
SD_D3: U1.19 (SD_DATA_3), U2.3 (/WP/IO2)
TXD: R5.1, U1.26 (U0TXD)
VCC: C3.1, C4.1, C7.1, GPIO0.1, GPIO2.1, MTDO.1, PWR.A, R3.2, R4.2, U1.1 (VDDA), U1.3 (VDD3P3), U1.4 (VDD3P3), U1.7 (CHIP_EN), U1.11 (VDDPST), U1.17 (VDDPST), U1.29 (VDDD), U1.30 (VDDA), U1.32 (EXT_RSTB), U2.8 (VCC), UEXT.1

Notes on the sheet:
SDIO
UART
FLASH
MTDO
GPIO0
GPIO2
MOD-WIFI-ESP8266, board revision A
OLIMEX LTD, PLOVDIV, BULGARIA 2014
https://www.olimex.com
This hardware design by Olimex LTD is licensed under a Creative Commons Attribution-ShareAlike 3.0 Unported License.

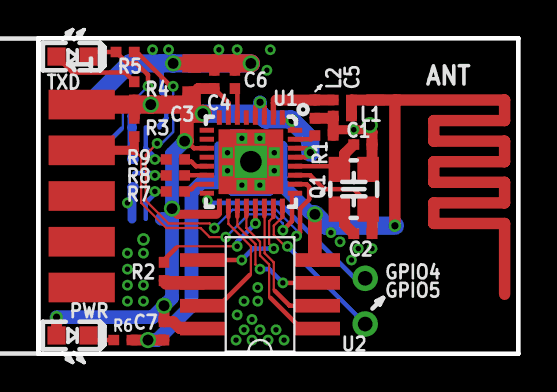
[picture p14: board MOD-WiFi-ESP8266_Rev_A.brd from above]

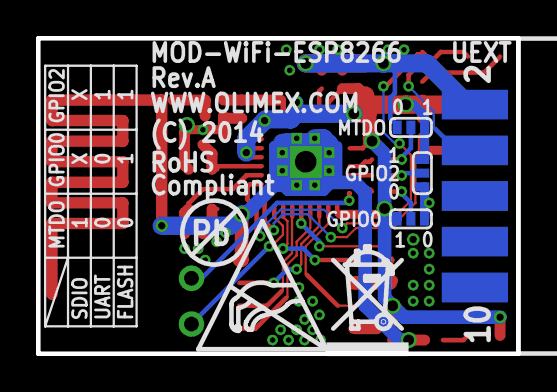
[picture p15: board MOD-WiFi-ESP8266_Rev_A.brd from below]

Board: 2 copper layers, 26.7 x 17.5 mm, 33 parts (7 on the bottom side), 28 nets.

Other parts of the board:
U$4: ESD_SYMBOL
U$6: PB_SMALL
U$7: RECYCLE_BIN1/8

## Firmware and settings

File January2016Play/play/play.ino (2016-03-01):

#include <Adafruit_NeoPixel.h>
#include <SoftwareSerial.h>

#include <SPI.h>
#include <SD.h>

const int rxd = 23;
const int txd = 22;

SoftwareSerial rfid_serial(rxd, txd); // RX, TX

const int spk_en_pin = 12;
const int spk_p_pin = PB6;
const int spk_n_pin = PB7;

const int motor_l_fwd = 14;
const int motor_l_back = 15;

const int motor_r_en = 13;
const int motor_r_fwd = PB3;
const int motor_r_back = PB5;

const int motor_r_pulse = 27;
const int motor_l_pulse = 28;

const int antenna_off_pin = PB4;

const int led_pin = 21;

const int sd_cs = 2; // 4??

static const int sDanceMovePeriodMillis = 100;

float glow_r = 255, glow_g = 255, glow_b = 255;

const int mic_pin = A0;
boolean dance_mode = false;
boolean repeat_mode = false;
int repeat_seq_start = -1, repeat_seq_end = -1;
int notes_in_row = 0;

enum ActionId{
  sIdNull=0,
  sIdTurnRight,
  sIdForward,
  sIdTurnLeft,
  sIdRepeat,
  sIdBackward,
  sIdDanceMode,
  sIdWait,
  sIdForClap,
  sIdReset, 
  sIdGo,
  sColorOrange,
  sColorRed,
  sColorGreen,
  sColorPurple,
  sColorBlue,
  sPlayDo,
  sPlayRe,
  sPlayMi,
  sPlayFa,
  sPlaySol,
  sPlayLa,
  sPlaySi,
};

const int sNotePeriods[] = {
  3830,
  3400,
  3038,
  2864,
  2550,
  2272,
  2028,
};


Adafruit_NeoPixel strip = Adafruit_NeoPixel(2, led_pin, NEO_GRB + NEO_KHZ800);

const uint32_t sNoteColors[] = {
  strip.Color(255,0,0),
  strip.Color(255,128,0),
  strip.Color(255,255,0),
  strip.Color(0,255,0),
  strip.Color(0,204,204),
  strip.Color(127,0,255),
  strip.Color(255,0,127),
  
};

const unsigned max_cards = 256;
unsigned n_cards_queued = 0;
unsigned cards_queued[max_cards];

void setup() {
  Serial.begin(9600);
  rfid_serial.begin(9600);

  pinMode(motor_l_fwd, OUTPUT);
  pinMode(motor_l_back, OUTPUT);

  pinMode(motor_r_en, OUTPUT);
  pinMode(motor_r_fwd, OUTPUT);
  pinMode(motor_r_back, OUTPUT);

  pinMode(motor_r_pulse, INPUT);
  pinMode(motor_l_pulse, INPUT);

  pinMode(spk_en_pin, OUTPUT);
  pinMode(spk_p_pin, OUTPUT);
  pinMode(spk_n_pin, OUTPUT);
  
  pinMode(antenna_off_pin, OUTPUT);
  
  pinMode(mic_pin, INPUT);

  pinMode(sd_cs, OUTPUT);
  
  TCCR1B = 0x01;   // Timer 1: PWM 9 & 10 @ 32 kHz
  TCCR2B = 0x01;   // Timer 2: PWM 3 & 11 @ 32 kHz
 
  strip.begin();
  strip.show(); // Initialize all pixels to 'off'

  Serial.println("-----"); 
}

#define DEFAULT_VOLUME 75

void my_tone(unsigned long for_millis, unsigned long period_micros, int volume=DEFAULT_VOLUME) {
  analogWrite(spk_en_pin, volume);
  for(const unsigned long sm=millis();(millis() - sm) < for_millis;) {
    digitalWrite(spk_p_pin, HIGH);
    delayMicroseconds(period_micros / 2);
    digitalWrite(spk_p_pin, LOW);  
    delayMicroseconds(10);

    digitalWrite(spk_n_pin, HIGH);
    delayMicroseconds(period_micros / 2);
    digitalWrite(spk_n_pin, LOW);
    delayMicroseconds(10);
  }
}

void stop_right()
{
  digitalWrite(motor_r_fwd, LOW);
  digitalWrite(motor_r_back, LOW);
  analogWrite(motor_r_en, 0);
}

void stop_left()
{
  analogWrite(motor_l_fwd, 0);
  analogWrite(motor_l_back, 0);
}

void stop() {
  digitalWrite(motor_r_en, HIGH);
  digitalWrite(motor_r_fwd, HIGH);
  digitalWrite(motor_r_back, HIGH);
  digitalWrite(motor_l_fwd, HIGH);
  digitalWrite(motor_l_back, HIGH);
}

void coast() {
  digitalWrite(motor_r_en, LOW);
  digitalWrite(motor_r_fwd, LOW);
  digitalWrite(motor_r_back, LOW);
  digitalWrite(motor_l_fwd, LOW);
  digitalWrite(motor_l_back, LOW);
}


const unsigned long sMinimumTimeBetweenPulses = 200;

// Try to filter any 32khz pwm
const unsigned long sMinimumPulseLength = 32;

class PulseCounter
{public:
   PulseCounter(int pin)
     : pin_(pin), 
       last_pulse_start_(0),
       pulses_(0), last_state_(digitalRead(pin))
   {
     //pinMode(rfid_pulse, OUTPUT);
   }
   
   void count() {
     const int state = digitalRead(pin_);
     
     if(state == LOW && last_state_ == HIGH) {
       // Pulse start
       const unsigned long now = micros();
       if((now - last_pulse_start_) > sMinimumTimeBetweenPulses) {
         last_state_ = LOW;
         this_pulse_start_ = now;
         /*
         if(pin_ == motor_r_pulse)
           digitalWrite(rfid_pulse, HIGH);
           */
       }
     } else if(state == HIGH && last_state_ == LOW) {
       // Pulse end
       last_state_ = HIGH;

       const unsigned long now = micros();
       if((now - this_pulse_start_) > sMinimumPulseLength) {
         ++pulses_;
         last_pulse_start_ = this_pulse_start_;
       }
/*
       if(pin_ == motor_r_pulse)
         digitalWrite(rfid_pulse, LOW);*/
     }
   }
   
   unsigned pulses()const {
     return pulses_;
   }
 private:
    const int pin_;
    
    int last_state_;
    unsigned pulses_;
    unsigned long last_pulse_start_;
    unsigned long this_pulse_start_;
};


void set_both_light_colors(uint32_t c) {
  strip.setPixelColor(0, c);
  strip.setPixelColor(1, c);
  strip.show();
}

void set_both_light_colors(uint8_t r, uint8_t g, uint8_t b) {
  const uint32_t c = strip.Color(r,g,b);
  set_both_light_colors(c);
}

void show_error() {
  set_both_light_colors(255, 0, 0);
  my_tone(500, 5000);
}

void set_move(const int l_sign, const int r_sign)
{
  coast();
  if(r_sign >= 0)
    digitalWrite(motor_r_fwd, HIGH);
  else
    digitalWrite(motor_r_back, HIGH);

  analogWrite(motor_r_en, 255);
  
  if(l_sign >= 0)
    analogWrite(motor_l_fwd, 255);
  else
    analogWrite(motor_l_back, 255);
}

boolean is_movement_action(unsigned action)
{
  return action == sIdForward ||
         action == sIdBackward ||
         action == sIdTurnLeft ||
         action == sIdTurnRight;
}

void start_dance_move(unsigned movement_action)
{
  if(movement_action != sIdNull) {
    switch(movement_action) {
      case sIdForward:
        set_move(1,1);
        break;
      case sIdBackward:
        set_move(-1,-1);
        break;
      case sIdTurnLeft:
        set_move(-1,1);
        break;
      case sIdTurnRight:
        set_move(1,-1);
        break;
    }
  }
}

void end_dance_move(unsigned movement_action)
{
  if(movement_action != sIdNull) {
    stop();
  }
}

void play_note(unsigned action_id, unsigned movement_action = sIdNull) {
  action_id = max(sPlayDo, min(sPlaySi, action_id));
  const unsigned long period = sNotePeriods[action_id - sPlayDo];
  set_both_light_colors(sNoteColors[action_id - sPlayDo]);

  my_tone(100, period);
  start_dance_move(movement_action);
  my_tone(sDanceMovePeriodMillis, period);
  end_dance_move(movement_action);
  my_tone(100, period);
}

unsigned get_action_for_card(uint32_t card)
{
  switch(card) {
    case 16522752:
    case 1986208512:
    case 3349243392:
    case 246244864:
    case 246248192:
    case 3468959232:
    case 2054252032:
    case 2054238976:
    case 1208098560:
    case 1408704512:
      return sPlayDo;
    case 131276288:
    case 596076032:
    case 545744384:
    case 127279872:
    case 1718820608:
    case 2364349952:
    case 1113858816:
    case 45704704:
    case 45704832:
    case 4175633920:
    case 364846592:
      return sPlayRe;
    case 1128472832:
    case 2929925632:
    case 516038144:
    case 516034304:
    case 1438719488:
    case 3740475008:
    case 3740474880:
    case 1400792576:
    case 81403392:
    case 1040654080:
      return sPlayMi;
    case 1101602304:
    case 111484416:
    case 1467377152:
    case 329457152:
    case 502472192:
    case 502472320:
    case 3539541504:
    case 3505987072:
    case 1692081664:
    case 1708858880:
    case 2348424704:
      return sPlayFa;
    case 817372672:
    case 3303087616:
    case 3336642048:
    case 3099139584:
    case 2340561664:
    case 3621807616:
    case 3621807872:
    case 2071553536:
    case 2071553792:
    case 3415500288:
    case 720445440:
      return sPlaySol;
    case 3164806656:
    case 3083432448:
    case 881601024:
    case 1175480576:
    case 2971101440:
    case 1181950720:
    case 1212817792:
    case 1212817664:
    case 652513024:
    case 652484096:
    case 1851138048:
    case 1851138304:
      return sPlayLa;
    case 3574144768:
    case 2251563264:
    case 3876003584:
    case 3859226368:
    case 1057431296:
    case 2533760768:
    case 1155163648:
    case 1188718080:
    case 3086753280:
    case 839458688:
    case 839458560:
      return sPlaySi;
    case 144449024:
    case 1262626304:
      return sIdTurnRight;
    case 2475845120:
    case 1447175680:
      return sIdForward;
    case 583624192:
    case 1413621248:
      return sIdTurnLeft;
    case 2917033472:
    case 1514284544:
      return sIdBackward;
    case 1547838976:
      return sIdDanceMode;
    case 2455276800:
    case 2772771584:
      return sIdReset;  
    case 2402900224:
    case 1982144768:
      return sIdGo;   
    // Colors
    case 1068768768:
      return sColorOrange;
    case 3470007808:
    case 1053498880:
      return sColorRed;
    case 4027457792:
      return sColorGreen;
    case 63118848:
    case 14489344:
    case 2885754624:
      return sColorPurple;
    case 3154059264:
    case 181149184:
      return sColorBlue;
    case 3761736960:
      return sIdWait;
    case 1866606080:
      return sIdForClap;
    case 1480730112:
      return sIdRepeat;
    default:
      return 0;
  }
} 

boolean is_note(unsigned action) {
  return action >= sPlayDo && action <= sPlaySi;
}

boolean is_special_action(unsigned action) {
  return action == sIdGo || action == sIdReset ||
          action == sColorOrange ||
          action == sColorRed ||
          action == sColorGreen ||
          action == sColorPurple ||
          action == sColorBlue;
}

void do_move(const int l_sign, const int r_sign, const int pulses)
{  
  digitalWrite(antenna_off_pin, HIGH);
  
  coast();
  
  const int mtr_r_speed = 255, mtr_l_speed = 240;
  const unsigned long sm = micros();
  PulseCounter count_left(motor_l_pulse);
  PulseCounter count_right(motor_r_pulse);

  long left_stop_t = 0, right_stop_t = 0;

  if(r_sign >= 0)
    digitalWrite(motor_r_fwd, HIGH);
  else
    digitalWrite(motor_r_back, HIGH);
  
  const int avg_speed = (mtr_r_speed + mtr_l_speed) / 2;

  analogWrite(motor_r_en, avg_speed);
  
  if(l_sign >= 0)
    analogWrite(motor_l_fwd, avg_speed);
  else
    analogWrite(motor_l_back, avg_speed);
  
  // Noise at signal start
 //delay(100);
 delay(50);

  Serial.println("-----");
  while(count_left.pulses() < pulses || count_right.pulses() < pulses) {
    count_left.count();
    count_right.count();
    const int iclp = count_left.pulses();
    const int icrp = count_right.pulses();
    
    if(abs(int(iclp) - int(icrp)) > 1) {
      if(iclp > icrp) {
        analogWrite(motor_r_en, mtr_r_speed);  
        if(l_sign >= 0)
          analogWrite(motor_l_fwd, 0);
        else
          analogWrite(motor_l_back, 0);
        
      } else {
        analogWrite(motor_r_en, 0);  
        if(l_sign >= 0)
          analogWrite(motor_l_fwd, mtr_l_speed);
        else
          analogWrite(motor_l_back, mtr_l_speed);
      }
      
    } else {
      analogWrite(motor_r_en, mtr_r_speed);   
      if(l_sign >= 0)
        analogWrite(motor_l_fwd, mtr_l_speed); 
      else
        analogWrite(motor_l_back, mtr_l_speed);
    }
    
  }
  stop();
  digitalWrite(antenna_off_pin, LOW);
}

void do_wait(int modifier_action)
{
  set_both_light_colors(0,0,0);
  const unsigned long glow_start = millis();
  switch(modifier_action) {
   case sIdForClap: {
     for(const unsigned long sm = millis();(millis() - sm) < 10000L && analogRead(mic_pin) < 800;) {
       const float t = float(millis() - glow_start) / 750.0f;
       const int intensity = int(255.0f * (0.5f + 0.5f * (sin(t * 2.0f * M_PI))));
       set_both_light_colors(intensity, intensity, intensity);
     }
     break;
   }
   default: {
     for(const unsigned long sm = millis();(millis() - sm) < 500L;) {
       const float t = float(millis() - glow_start) / 750.0f;
       const int intensity = int(255.0f * (0.5f + 0.5f * (sin(t * 2.0f * M_PI))));
       set_both_light_colors(intensity, intensity, intensity);
     }
    break;
   }
  }
}

void go_start()
{
  set_both_light_colors(64,64,0);
  my_tone(300, 1250);
  set_both_light_colors(0,0,0);
  delay(200);
  set_both_light_colors(255,255,0);
  my_tone(300, 1250);
  set_both_light_colors(0,0,0);
  delay(200);
  set_both_light_colors(0,255,0);
  my_tone(300, 800);
  set_both_light_colors(0,0,0);

  // Modes set-up  
  dance_mode = false;
  repeat_mode = false;
  
  // Measure detection
  notes_in_row = 0;
}

void do_go()
{
  if(n_cards_queued == 0) {
    set_both_light_colors(255,0,0);
    my_tone(750, 6000);
    return;
  }

  go_start();

//  const int straight_ticks = 340;  
//  const int turn_ticks = 138;
// R35 
  const int straight_ticks = 400;
  const int turn_ticks = 150;
  
  int jumped_from_idx = -1;
  
  boolean saved_dance_mode = false;
  
  for(unsigned card_idx=0;card_idx<n_cards_queued;++card_idx) {
    const unsigned card = cards_queued[card_idx];
    if(card_idx >= repeat_seq_start && 
       ((repeat_seq_end < 0) || (card_idx <= repeat_seq_end))) {
      if(!repeat_mode)
        continue;
      if(card_idx == repeat_seq_start)
        continue;
      if(card_idx == repeat_seq_end) {
        card_idx = jumped_from_idx;  // Increment will move to the next card
        repeat_mode = false;
        dance_mode = saved_dance_mode;
        continue;
      }
    }
    set_both_light_colors(200,200,200);
    if(dance_mode && is_movement_action(card)) {
      start_dance_move(card);
      delay(sDanceMovePeriodMillis);
      end_dance_move(card);
    } else {
      switch(card) {
        case sIdForward:
          do_move(1,1,straight_ticks);
          break;
        case sIdBackward:
          do_move(-1,-1,straight_ticks);
          break;
        case sIdTurnLeft:
          do_move(-1,1,turn_ticks);
          break;
        case sIdTurnRight:
          do_move(1,-1,turn_ticks);
          break;
        case sIdDanceMode:
          dance_mode = !dance_mode;
          break;
        case sIdRepeat:
          Serial.print("Hit repeat card, jumping to ");
          Serial.println(repeat_seq_start);
          jumped_from_idx = card_idx;
          card_idx = repeat_seq_start;
          repeat_mode = true;
          saved_dance_mode = dance_mode;
          dance_mode = false;
          break;
        case sIdWait:
        {
          int modifier_action = sIdNull;
          if(card_idx < (n_cards_queued-1) && is_action_modifier(cards_queued[card_idx+1])) {
            modifier_action = cards_queued[++card_idx];
          }
          do_wait(modifier_action);
          break;
        }
        default:
        {
          if(is_note(card)) {
            int next_movement_action = sIdNull;
            if(dance_mode && card_idx < (n_cards_queued-1) && is_movement_action(cards_queued[card_idx+1])) {
              next_movement_action = cards_queued[++card_idx];
            }
            play_note(card, next_movement_action);
          }
          break;
        }
      }
    }
    set_both_light_colors(0,0,0);
    //delay(300);
    
    // Ignore cards queued during action
    while(rfid_serial.available())
      rfid_serial.read();

    unsigned long pause_millis = 300;

    if(is_note(card))
      ++notes_in_row;
    else
      notes_in_row = 0;
    
    if(notes_in_row > 0) {
      if(notes_in_row % 4 == 0)
        pause_millis = 300;
      else
        pause_millis = 100;
    }
      
    boolean pause_mode = false;
    unsigned long glow_start = millis();

    for(const unsigned long smillis = millis();pause_mode || ((millis() - smillis) < pause_millis);) {
      if(pause_mode) {
        const float t = float(millis() - glow_start) / 750.0f;
        const int intensity = int(255.0f * (0.5f + 0.5f * (sin(t * 2.0f * M_PI))));
        set_both_light_colors(intensity, intensity, intensity);
      }
      if(rfid_serial.available()) {
        uint32_t card_id = 0;
        if(4 == rfid_serial.readBytes((char*)&card_id, 4)) {
          Serial.print("card between actions: ");
          Serial.println(card_id);
          const int action_id = get_action_for_card(card_id);
          if(action_id == sIdReset) {
            do_reset();
            goto finished_actions;
          } else if(action_id == sIdWait) {
            if(!pause_mode) {
              // TODO: Jingle?
              pause_mode = true;
              glow_start = millis();
            } else {
              pause_mode = false;
              set_both_light_colors(0,0,0);
            }
          } else if(action_id == sIdGo) {
            card_idx = ~0;  // Loop will increment
            go_start();
            break;
          }
        }
      }
    }
  }
 finished_actions:
  // Ignore cards queued during action
  while(rfid_serial.available())
    rfid_serial.read();
 }

void do_reset()
{
  n_cards_queued = 0;
  dance_mode = false;
  repeat_mode = false;
  repeat_seq_start = repeat_seq_end = -1;
  const float tmax = 2.75f;
  for(float t=0;t<tmax;t+=0.1f) {
    const float n = sin(t * 2 * M_PI);
    const float scale = 1.0f - (t / tmax);
    my_tone(100, 750 + 750 * (0.5f + 0.5f * n), scale * DEFAULT_VOLUME);
    set_both_light_colors(max(0, n*scale*255),0,max(0, -n*scale*255));
  }
}

void dance_mode_jingle()
{
  play_note(sPlayFa, sIdNull);
  delay(50);
  play_note(sPlayRe, sIdNull);
}
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
void loop() {
  static boolean saved_dance_mode = false;
  
  // Glow
  const unsigned long glow_period_micros = (dance_mode || repeat_mode) ? 200000L : 2000000L;
  static unsigned long last_glow_micros = micros();
  static unsigned long glow_t_micros = 0;
  
  // Limit glow frequency so we don't interfere with RFID antenna
  {
    const unsigned long m = micros();
    const unsigned long glow_t_micros_offset = m - last_glow_micros;
    glow_t_micros += glow_t_micros_offset;
    last_glow_micros = m;
    float glow_t = float(glow_t_micros) / glow_period_micros;
    
    float glow_n = 0.5f - 0.5f*cos(glow_t * 2.0f * M_PI);
    if(repeat_mode && !dance_mode) {
      if(fmod(glow_t, 4.0f) >= 2.0f)
        glow_n = 0;
    }

    set_both_light_colors(glow_n * glow_r, glow_n * glow_g, glow_n * glow_b);
  }
  
  // "Blink" the antenna when waiting for commands, to avoid interfering with
  // nearby Plobots
  static unsigned long last_antenna_millis = millis();
  const unsigned long now = millis();
  static boolean antenna_mode = false;
  if((now - last_antenna_millis) >= 225) {
     last_antenna_millis = now;
     antenna_mode = (random(3) != 0);
     digitalWrite(antenna_off_pin, antenna_mode ? HIGH : LOW);
  }
  if((now - last_antenna_millis) > 75) {
     digitalWrite(antenna_off_pin, antenna_mode ? LOW : HIGH);
  }
  
  // Card scanning
  if (rfid_serial.available()) {
    uint32_t card_id = 0;
    if(4 == rfid_serial.readBytes((char*)&card_id, 4)) {
      Serial.print("card: ");
      Serial.println(card_id);
      const int action_id = get_action_for_card(card_id);
      if(!action_id)
      {
        // Ignore
        // TODO: Figure out why this happens
        /*
        show_error();
        delay(100);
        show_error();
        */
      }
      else
      {
        Serial.print("action: ");
        Serial.println(action_id);
        
        if(is_special_action(action_id)) {
          switch(action_id) {
            case sIdGo:
              do_go();
              break;
            case sIdReset:
              do_reset();
              break;
            case sColorOrange:
              glow_r = 255.0f;
              glow_g = 165.0f;
              glow_b = 0.0f;
              break;
            case sColorRed:
              glow_r = 255.0f;
              glow_g = 0.0f;
              glow_b = 0.0f;
              break;
            case sColorGreen:
              glow_r = 0.0f;
              glow_g = 255.0f;
              glow_b = 0.0f;
              break;
            case sColorPurple:
              glow_r = 128.0f;
              glow_g = 0.0f;
              glow_b = 128.0f;
              break;
            case sColorBlue:
              glow_r = 0.0f;
              glow_g = 0.0f;
              glow_b = 255.0f;
              break;
            default:
              if(is_note(action_id)) {
                play_note(action_id);
              }
              break;
          }
        } else {
          if(n_cards_queued == max_cards) {
            show_error();
          } else if(is_action_modifier(action_id) && 
                  (n_cards_queued == 0 || !is_modifiable_action(cards_queued[n_cards_queued-1]))) {
            show_error();
          }
          else
          {
            // Record card
           cards_queued[n_cards_queued++] = action_id;
            
            if(is_note(action_id)) {
              play_note(action_id);
            } else if(action_id == sIdDanceMode) {
              dance_mode = !dance_mode;
              if(dance_mode)
                dance_mode_jingle();
              else
                scan_success_jingle();
            } else if(action_id == sIdRepeat) {
              if(repeat_seq_end < 0) {
                subroutine_jingle(repeat_mode);
                if(!repeat_mode) {
                  repeat_mode = true;
                  repeat_seq_start = n_cards_queued-1;
                  saved_dance_mode = dance_mode;
                  dance_mode = false;
                  Serial.print("Sequence started at ");
                } else {
                  repeat_mode = false;
                  repeat_seq_end = n_cards_queued-1;
                  dance_mode = saved_dance_mode;
                  
                  Serial.print("Sequence ended ");
                  Serial.print(repeat_seq_start);
                  Serial.print(" ");
                  Serial.println(repeat_seq_end);
                }
              } else {
                scan_success_jingle();
              }
            } else {
              scan_success_jingle();
            }
          }
        }
      }
    }
    // One card at a time
    while(rfid_serial.available())
      rfid_serial.read();
  }
}

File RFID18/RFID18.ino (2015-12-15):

/*
 Plobot OS

 This code uses bitlash as an interpreter (thanks BillRoy http://bitlash.net)
 It's base is to execute commands that are stored in a buffer.
 Input of commands might be RFID for young kids or through serial protocol over WIFI

 The circuit:
 * LED attached from digital pin 13, 12 and 9  //note that on current ATmega644 there is no PWM output.
 * Anode to VCC (resistors of 330ohms)

 * RFID attached to Serial

 Created  28 March 2015
 Modified 02 April 2015\
 Last Update 04 July 2015
 By Rodolfo Cossovich [rudi]


 http://plobotics.org

 This example code is in the public domain.

 */
#define MOTOR
#define ENCODERS 1
#define MUSIC

#include <SM.h>
#include "bitlash.h"


#ifdef MOTOR
#include <DCMotor.h>

int M0EN = 12;
int M01  = 19;
int M02 =  20;

int M1EN =  13;
int M11 =  21;
int M12 =  22;

DCMotor motor0(M0EN, M01, M02);
DCMotor motor1(M1EN, M11, M12);
#endif

#define RED_LED    3//13
#define BLUE_LED   4//12
#define GREEN_LED  14//9

#define RFID_PACK  10

#define VCC_LED  2

#ifdef ENCODERS
#define ENCODER_T 250
#define speedMotors 80.0
#define LEVEL_ENCODER 255

#define INTERRUPTS 0

#define ENCODER1 1
#define ENCODER2 0

// ideally these would be flags and with assembler we increment the counter that is refreshed in main loop...
volatile unsigned long int encoderCounter1 = 0;   // counter for the times the encoder changed state
volatile byte encoderState1 = 0;         // current state of encoder as read by interrrupt service
volatile byte lastEncoderState1 = 0;     // previous state of encoder
volatile unsigned long int encoderCounter2 = 0;   // counter for the times the encoder changed state
volatile byte encoderState2 = 0;
volatile byte lastEncoderState2 = 0;

volatile int stepsA = 0;
volatile int stepsB = 0;
#endif

#ifdef MUSIC
#define SPEAKER 15

#define OCTAVE_OFFSET 0

// These values can also be found as constants in the Tone library (Tone.h)
int notes[] = {
  0,
  262, 277, 294, 311, 330, 349, 370, 392, 415, 440, 466, 494,
  523, 554, 587, 622, 659, 698, 740, 784, 831, 880, 932, 988,
  1047, 1109, 1175, 1245, 1319, 1397, 1480, 1568, 1661, 1760, 1865, 1976,
  2093, 2217, 2349, 2489, 2637, 2794, 2960, 3136, 3322, 3520, 3729, 3951
};

//char *song = "The Simpsons:d=4,o=5,b=160:c.6,e6,f#6,8a6,g.6,e6,c6,8a,8f#,8f#,8f#,2g,8p,8p,8f#,8f#,8f#,8g,a#.,8c6,8c6,8c6,c6";
//char *song = "Indiana:d=4,o=5,b=250:e,8p,8f,8g,8p,1c6,8p.,d,8p,8e,1f,p.,g,8p,8a,8b,8p,1f6,p,a,8p,8b,2c6,2d6,2e6,e,8p,8f,8g,8p,1c6,p,d6,8p,8e6,1f.6,g,8p,8g,e.6,8p,d6,8p,8g,e.6,8p,d6,8p,8g,f.6,8p,e6,8p,8d6,2c6";
//char *song = "TakeOnMe:d=4,o=4,b=160:8f#5,8f#5,8f#5,8d5,8p,8b,8p,8e5,8p,8e5,8p,8e5,8g#5,8g#5,8a5,8b5,8a5,8a5,8a5,8e5,8p,8d5,8p,8f#5,8p,8f#5,8p,8f#5,8e5,8e5,8f#5,8e5,8f#5,8f#5,8f#5,8d5,8p,8b,8p,8e5,8p,8e5,8p,8e5,8g#5,8g#5,8a5,8b5,8a5,8a5,8a5,8e5,8p,8d5,8p,8f#5,8p,8f#5,8p,8f#5,8e5,8e5";
//char *song = "Entertainer:d=4,o=5,b=140:8d,8d#,8e,c6,8e,c6,8e,2c.6,8c6,8d6,8d#6,8e6,8c6,8d6,e6,8b,d6,2c6,p,8d,8d#,8e,c6,8e,c6,8e,2c.6,8p,8a,8g,8f#,8a,8c6,e6,8d6,8c6,8a,2d6";
//char *song = "Muppets:d=4,o=5,b=250:c6,c6,a,b,8a,b,g,p,c6,c6,a,8b,8a,8p,g.,p,e,e,g,f,8e,f,8c6,8c,8d,e,8e,8e,8p,8e,g,2p,c6,c6,a,b,8a,b,g,p,c6,c6,a,8b,a,g.,p,e,e,g,f,8e,f,8c6,8c,8d,e,8e,d,8d,c";
//char *song = "Xfiles:d=4,o=5,b=125:e,b,a,b,d6,2b.,1p,e,b,a,b,e6,2b.,1p,g6,f#6,e6,d6,e6,2b.,1p,g6,f#6,e6,d6,f#6,2b.,1p,e,b,a,b,d6,2b.,1p,e,b,a,b,e6,2b.,1p,e6,2b.";
//char *song = "Looney:d=4,o=5,b=140:32p,c6,8f6,8e6,8d6,8c6,a.,8c6,8f6,8e6,8d6,8d#6,e.6,8e6,8e6,8c6,8d6,8c6,8e6,8c6,8d6,8a,8c6,8g,8a#,8a,8f";
//char *song = "20thCenFox:d=16,o=5,b=140:b,8p,b,b,2b,p,c6,32p,b,32p,c6,32p,b,32p,c6,32p,b,8p,b,b,b,32p,b,32p,b,32p,b,32p,b,32p,b,32p,b,32p,g#,32p,a,32p,b,8p,b,b,2b,4p,8e,8g#,8b,1c#6,8f#,8a,8c#6,1e6,8a,8c#6,8e6,1e6,8b,8g#,8a,2b";
//char *song = "Bond:d=4,o=5,b=80:32p,16c#6,32d#6,32d#6,16d#6,8d#6,16c#6,16c#6,16c#6,16c#6,32e6,32e6,16e6,8e6,16d#6,16d#6,16d#6,16c#6,32d#6,32d#6,16d#6,8d#6,16c#6,16c#6,16c#6,16c#6,32e6,32e6,16e6,8e6,16d#6,16d6,16c#6,16c#7,c.7,16g#6,16f#6,g#.6";
//char *song = "MASH:d=8,o=5,b=140:4a,4g,f#,g,p,f#,p,g,p,f#,p,2e.,p,f#,e,4f#,e,f#,p,e,p,4d.,p,f#,4e,d,e,p,d,p,e,p,d,p,2c#.,p,d,c#,4d,c#,d,p,e,p,4f#,p,a,p,4b,a,b,p,a,p,b,p,2a.,4p,a,b,a,4b,a,b,p,2a.,a,4f#,a,b,p,d6,p,4e.6,d6,b,p,a,p,2b";
//char *song = "StarWars:d=4,o=5,b=45:32p,32f#,32f#,32f#,8b.,8f#.6,32e6,32d#6,32c#6,8b.6,16f#.6,32e6,32d#6,32c#6,8b.6,16f#.6,32e6,32d#6,32e6,8c#.6,32f#,32f#,32f#,8b.,8f#.6,32e6,32d#6,32c#6,8b.6,16f#.6,32e6,32d#6,32c#6,8b.6,16f#.6,32e6,32d#6,32e6,8c#6";
//char *song = "GoodBad:d=4,o=5,b=56:32p,32a#,32d#6,32a#,32d#6,8a#.,16f#.,16g#.,d#,32a#,32d#6,32a#,32d#6,8a#.,16f#.,16g#.,c#6,32a#,32d#6,32a#,32d#6,8a#.,16f#.,32f.,32d#.,c#,32a#,32d#6,32a#,32d#6,8a#.,16g#.,d#";
//char *song = "TopGun:d=4,o=4,b=31:32p,16c#,16g#,16g#,32f#,32f,32f#,32f,16d#,16d#,32c#,32d#,16f,32d#,32f,16f#,32f,32c#,16f,d#,16c#,16g#,16g#,32f#,32f,32f#,32f,16d#,16d#,32c#,32d#,16f,32d#,32f,16f#,32f,32c#,g#";
//char *song = "A-Team:d=8,o=5,b=125:4d#6,a#,2d#6,16p,g#,4a#,4d#.,p,16g,16a#,d#6,a#,f6,2d#6,16p,c#.6,16c6,16a#,g#.,2a#";
//char *song = "Flinstones:d=4,o=5,b=40:32p,16f6,16a#,16a#6,32g6,16f6,16a#.,16f6,32d#6,32d6,32d6,32d#6,32f6,16a#,16c6,d6,16f6,16a#.,16a#6,32g6,16f6,16a#.,32f6,32f6,32d#6,32d6,32d6,32d#6,32f6,16a#,16c6,a#,16a6,16d.6,16a#6,32a6,32a6,32g6,32f#6,32a6,8g6,16g6,16c.6,32a6,32a6,32g6,32g6,32f6,32e6,32g6,8f6,16f6,16a#.,16a#6,32g6,16f6,16a#.,16f6,32d#6,32d6,32d6,32d#6,32f6,16a#,16c.6,32d6,32d#6,32f6,16a#,16c.6,32d6,32d#6,32f6,16a#6,16c7,8a#.6";
//char *song = "Jeopardy:d=4,o=6,b=125:c,f,c,f5,c,f,2c,c,f,c,f,a.,8g,8f,8e,8d,8c#,c,f,c,f5,c,f,2c,f.,8d,c,a#5,a5,g5,f5,p,d#,g#,d#,g#5,d#,g#,2d#,d#,g#,d#,g#,c.7,8a#,8g#,8g,8f,8e,d#,g#,d#,g#5,d#,g#,2d#,g#.,8f,d#,c#,c,p,a#5,p,g#.5,d#,g#";
char *song = "Gadget:d=16,o=5,b=50:32d#,32f,32f#,32g#,a#,f#,a,f,g#,f#,32d#,32f,32f#,32g#,a#,d#6,4d6,32d#,32f,32f#,32g#,a#,f#,a,f,g#,f#,8d#";
//char *song = "Smurfs:d=32,o=5,b=200:4c#6,16p,4f#6,p,16c#6,p,8d#6,p,8b,p,4g#,16p,4c#6,p,16a#,p,8f#,p,8a#,p,4g#,4p,g#,p,a#,p,b,p,c6,p,4c#6,16p,4f#6,p,16c#6,p,8d#6,p,8b,p,4g#,16p,4c#6,p,16a#,p,8b,p,8f,p,4f#";
//char *song = "MahnaMahna:d=16,o=6,b=125:c#,c.,b5,8a#.5,8f.,4g#,a#,g.,4d#,8p,c#,c.,b5,8a#.5,8f.,g#.,8a#.,4g,8p,c#,c.,b5,8a#.5,8f.,4g#,f,g.,8d#.,f,g.,8d#.,f,8g,8d#.,f,8g,d#,8c,a#5,8d#.,8d#.,4d#,8d#.";
//char *song = "LeisureSuit:d=16,o=6,b=56:f.5,f#.5,g.5,g#5,32a#5,f5,g#.5,a#.5,32f5,g#5,32a#5,g#5,8c#.,a#5,32c#,a5,a#.5,c#.,32a5,a#5,32c#,d#,8e,c#.,f.,f.,f.,f.,f,32e,d#,8d,a#.5,e,32f,e,32f,c#,d#.,c#";
//char *song = "MissionImp:d=16,o=6,b=95:32d,32d#,32d,32d#,32d,32d#,32d,32d#,32d,32d,32d#,32e,32f,32f#,32g,g,8p,g,8p,a#,p,c7,p,g,8p,g,8p,f,p,f#,p,g,8p,g,8p,a#,p,c7,p,g,8p,g,8p,f,p,f#,p,a#,g,2d,32p,a#,g,2c#,32p,a#,g,2c,a#5,8c,2p,32p,a#5,g5,2f#,32p,a#5,g5,2f,32p,a#5,g5,2e,d#,8d";


#define isdigit(n) (n >= '0' && n <= '9')

#endif
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

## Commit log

2015-12-15 Fork from Sean
    [BOT-CPU.SchDoc, test_1.csv, test_2.csv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]
2015-12-26 New PCB stuff
    [BOT-TOP.SchDoc, CPU-V4e_antenna_2.PcbDoc, antenna_test.PcbDoc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]
2015-12-27 - Placement 80% complete
    [main_pcb.SchDoc, speaker.SchDoc, test_5.PcbDoc]
2015-12-27 - Power routing nearly complete
    [main_pcb.PrjPCB, main_pcb.SchDoc, mic.SchDoc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]
2015-12-27 - Progress, rename
    [main_pcb.PcbDoc, main_pcb.PrjPCB, test_5.PcbDoc]
2015-12-28 - Progress
    [main_pcb.PcbDoc, main_pcb.SchDoc, rfid.SchDoc]
2015-12-28 - Fixed schematic error
    [main_pcb.PcbDoc, main_pcb.SchDoc]
2015-12-28 - RFID Routed
    [main_pcb.PcbDoc]
2015-12-28 - Pour beneath micro
    [main_pcb.PcbDoc]
2015-12-28 Routing Routing Routing
    [main_pcb.PcbDoc]
2015-12-28 - Auto routed almost all remaining signals
    [main_pcb.PcbDoc]
2015-12-28 - Routing continues
    [main_pcb.PcbDoc]
2015-12-28 - Routing finished: needs checks
    [main_pcb.PcbDoc, main_pcb.PrjPCB]
2015-12-29 - Removed auto router garbage from power network
    [main_pcb.PcbDoc]
2015-12-29 Fixed logic and motor driver power separation
    [main_pcb.PcbDoc]
2015-12-29 - More power network tweaks
    [main_pcb.PcbDoc]
2015-12-29 - Fixed rules violations
    [main_pcb.PcbDoc]
2015-12-29 - Fixed silk screen
    [components.PcbLib, main_pcb.PcbDoc]
2015-12-29 - Beginning antenna
    [main_pcb.PcbDoc, main_pcb.PrjPCB, main_pcb.SchDoc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]
2015-12-29 - Defined antenna geometry
    [main_pcb.PcbDoc]
2015-12-29 - Refined geometry
    [main_pcb.PcbDoc]
2015-12-29 - Antenna progress
    [main_pcb.PcbDoc]
2015-12-29 - Shielded crystal
    [main_pcb.PcbDoc]
2015-12-29 - First layer of antenna finished
    [main_pcb.PcbDoc]
2015-12-29 - Antenna finished
    [main_pcb.PcbDoc]
2015-12-29 - Antenna fixes
    [main_pcb.PcbDoc]
2015-12-29 - Routed center LEDs
    [main_pcb.PcbDoc]
2015-12-29 - Final fixes
    [main_pcb.PcbDoc]
2016-01-12 - PCB changes
    [main_pcb.PcbDoc, main_pcb.SchDoc, motor.SchDoc]
2016-01-12 - New board stuff
2016-01-15 - Consistent squares!
    [motor.SchDoc]
2016-01-22 - Reset during actions
    [play.ino]
2016-01-25 Sample Files for Sound Workshop
2016-01-28 - Check in motor test
2016-02-02 - Schematic changes working toward new PCB
    [main_pcb.SchDoc]
2016-02-15 Workshop Financials
    Initial Upload
    [Plobot Playground Accounting.xlsx]
2016-02-16 Fix for Bug #20
    [play.ino]
2016-02-22 Added files via upload
    Latest Updates
    [Plobot.Playground.Accounting.xlsx]
2016-03-01 - New schematic
    [components.PcbLib, components.SchLib, main_pcb.PrjPCB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]
2016-05-30 - New PCB schematic
    [components.PcbLib, main_pcb.PrjPCB, main_pcb.SchDoc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]
2016-06-14 - Progress on new PCB
    [components.PcbLib, components.SchLib, main_pcb.PrjPCB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]
2016-06-23 PCB with RFID integrated
    [components.PcbLib, components.SchLib, main_pcb.PrjPCB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]
2016-07-02 - Accelerometer test
2016-07-06 - PCB ready to go to factory
    [main_pcb_new_id.PcbDoc]
2016-07-07 - Final v1 PCB to factory
    [Plobot_V3_1.csv, main_pcb_new_id.PcbDoc]
2016-07-13 - Saving Open ESP board
    [MOD-WiFi-ESP8266_Rev_A.brd, MOD-WiFi-ESP8266_Rev_A.sch]
2016-07-13 - Latest PCB
    [main_pcb_new_id.PcbDoc]
2016-07-19 - BOM cost reduction concept board
    [Plobot_V3_1.csv, cheap.PrjPCB, components.PcbLib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]
2016-07-19 - RFID test improvement for reading codes
    [bom.csv, test.PcbDoc]
2016-07-24 New PCM audio, not tweaked
    - Updated audio test
    - Created programs for writing to Plobot’s flash chip
2016-07-29 - Fix for initial arm position
    [Main_19JUL2016.ino]
2016-08-01 - Fix for motor drivers heating up
    [Main_19JUL2016.ino]
2016-08-03 - Gyroscope turn test
2016-08-10 Correct RFID card writing code
    [RFID_write.ino]
2016-08-10 - Schematic changes to BOM cost reduction test
    [test.SchDoc]
2016-08-10 - Old PCB DXF
    [pcb_mechanical.DXF]
2016-08-10 - Match color names to current cards
2016-08-12 Low battery stop
2016-08-12 - Print battery level
2016-08-12 - Show battery level on start
2016-08-12 - Green for full battery - No double light up
2016-08-15 - Removed debug print
2016-08-15 #32 Power ramp to avoid stalls
2016-08-15 #32 Added power ramp for turns
2016-08-15 - LED test fix
    [LEDs.ino]
2016-08-15 - Possible change for card scanning freeze edge case
2016-09-25 - Starting changes to PCB
    [components.PcbLib, components.SchLib, main_pcb.SchDoc]
2016-10-13 15cm distance
2017-02-19 new version for the PCB
    [audio.SchDoc, connections.SchDoc, cpu.SchDoc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]
2018-04-25 removed irrelevant
    [Plobot Playground Accounting.xlsx, Plobot.Playground.Accounting.xlsx]
2018-04-25 Added tests previous to production
    [Winbond Flash Instructions - Comparison.xlsx]

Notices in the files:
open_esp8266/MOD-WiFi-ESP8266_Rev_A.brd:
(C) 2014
